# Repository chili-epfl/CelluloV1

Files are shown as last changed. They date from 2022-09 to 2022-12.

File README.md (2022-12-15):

# Cellulo V1

Cellulo is a social, cognitive-motor assistive tabletop robot, created in the CHILI Lab at EPFL. It was born under the efforts of multiple collaborators, with special remarks to [Ayberk Özgür](https://github.com/ayberkozgur) who presented it as his [Ph.D. thesis](https://infoscience.epfl.ch/record/234374?ln=en).

<p align="center">
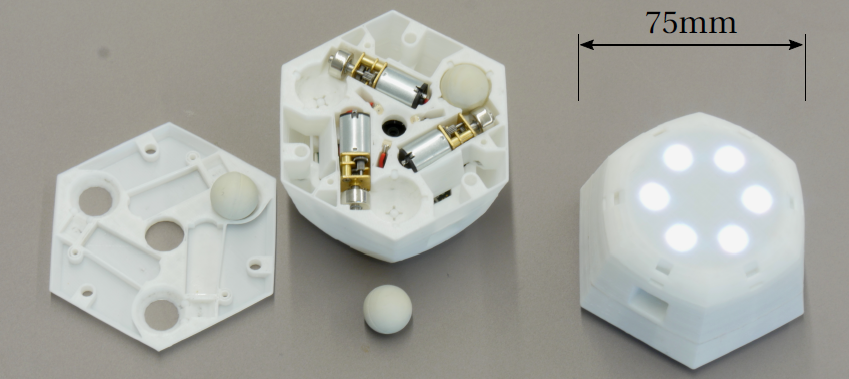
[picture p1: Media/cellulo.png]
  
</p>

## Features

- Holonomic movement
- Haptic feedback
- Sub-mm localization
- LED indicators
- Touch sensor
- Wireless connectivity

## Links

Information about how to work with Cellulo and installations can be found in the [wiki](https://github.com/chili-epfl/cellulo/wiki/Cellulo-V1)

To work with Cellulo it is necesary to install [Cellulo qml plugin](https://github.com/chili-epfl/cellulo-qml-plugin)

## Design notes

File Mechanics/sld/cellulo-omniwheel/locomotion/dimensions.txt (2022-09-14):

"wheel_dia"=30
"wheel_rim_room"=1
"miniwheel_top_bottom_room"=0.7
"miniwheel_side_room"=0.7
"miniwheel_axle_dia"=1.4
"miniwheel_axle_holding_room"=0.5
"rim_extra_width"=0.3
"miniwheel_neck_width"=0.8
"middle_thickness"=8.5
"motor_axle_dia"=3
"motor_axle_room"=0.1
"motor_axle_notch_thickness"=2.5
"mate_room"=0.10
"vertical_mate_room"=0.1
"miniwheel_base_dia"=7.39
"miniwheel_axle_room"=0.1
"miniwheel_rubber_thickness"=1

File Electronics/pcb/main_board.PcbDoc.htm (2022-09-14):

Reporting Options

# File in Previous Format

Date | : | 20/05/2022
Time | : | 18:22:09
Filename | : | C:\Users\VIctor work\Documents\EPFL\CHILI\cellulo-electronics\pcb\main_board.PcbDoc

Version | Warning

This file was generated by an earlier version of the software

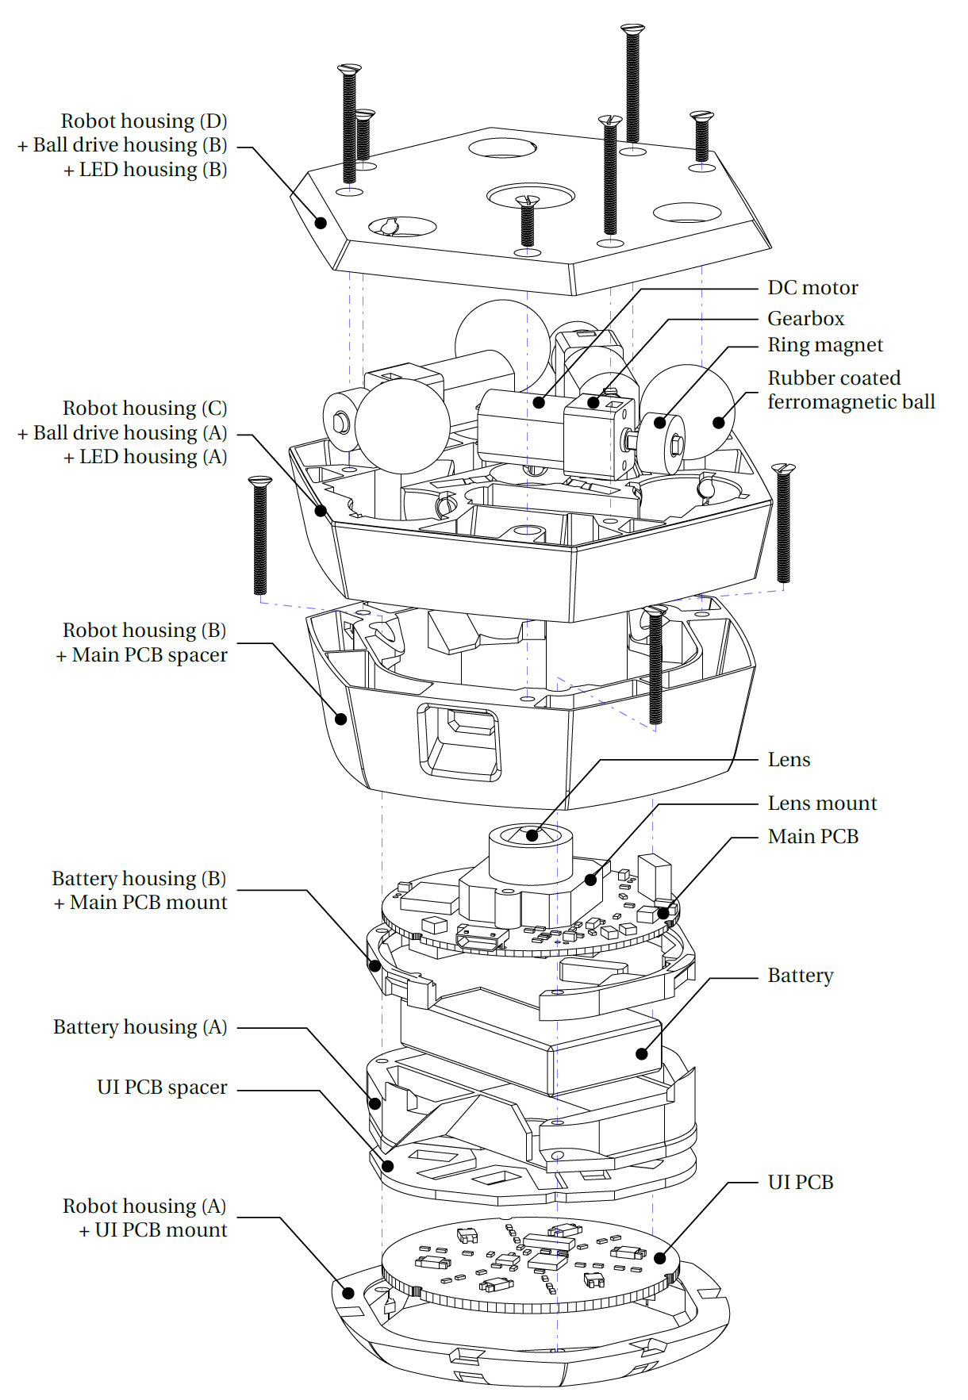
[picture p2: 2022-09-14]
Media/exploited view.png

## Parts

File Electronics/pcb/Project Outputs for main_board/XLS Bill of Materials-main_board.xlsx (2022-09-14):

Designator | Comment | Package | Quantity | Place_YES/NO | Provided_by_customer_YES/NO | Remarks_customer
BAT1 | Battery_1S | WAGO 2059-302 | 1 | YES | YES
C1, C2, C3, C4, C5, C6, C21, C22, C23, C24 | 0.1uF | 1608[0603]_M | 10 | YES | YES
C7, C8, C9 | 47uF | 2012[0805]_M | 3 | YES | YES
C10, C11, C13, C16, C17 | 4.7uF, 10V | 1608[0603]_M | 5 | YES | YES
C12, C15 | 10uF, 10V | 1608[0603]_M | 2 | YES | YES
C14 | 0.1uF, 10V | 1608[0603]_M | 1 | YES | YES
C18, C19, C20 | Unpopulated | 2012[0805]_M | 3 | NO
IC1 | RN42-I/RM | RN42 | 1 | YES | YES
IC2 | PIC32MZ1024ECG064-I/PT | TQFP-64_M | 1 | YES | YES
IC3, IC4, IC5 | BD6210HFP | HRP7_N | 3 | YES | YES
IC6 | MT9V034C12STM | CLCC-48_m | 1 | YES | YES
IC7 | MCP73871-2CCI/ML | QFN-20_M | 1 | YES | YES
IC8 | LM3671MF-3.3 | SOT23-5_N | 1 | YES | YES
IC9 | BQ29700DSET | WSON-6_M | 1 | YES | YES
IC10 | LP2980-AIM5-3.3 | SOT23-5_N | 1 | YES | YES
L1 | SRN2512-2R2M | 2520[1008]_N | 1 | YES | YES
LED1, LED2, LED3 | Unpopulated | PLCC2_WITH_HEATSINK | 3 | NO
M1, M2, M3 | Unpopulated | CABLE-TERMINAL1x2 | 3 | NO
P1 | Connector 5 | BM05B-SRSS_N | 1 | YES | YES
P2 | Connector 12 | FH33-12S-0.5SH_N | 1 | YES | YES
P3 | MicroUSB2.0 | USB3076_M | 1 | YES | YES
Q1 | BSS138BK | SOT23-3_N | 1 | YES | YES
Q2, Q3 | Unpopulated | SOT23-3_N | 2 | NO
Q4, Q5 | CSD17527Q5A | PG-TDSON-8_MOSFET_M | 2 | YES | YES
R1, R2, R3, R4, R5, R8, R10, R11, R12, R13, R14, R15, R16, R19, R24, R28, R29, R30, R34, R43 | 10K | 1608[0603]_M | 20 | YES | YES
R6, R7 | 1K5 | 1608[0603]_M | 2 | YES | YES
R9, R36, R37, R39, R40, R44 | Unpopulated | 1608[0603]_M | 6 | NO
R17, R18 | 1K | 1608[0603]_M | 2 | YES | YES
R20, R21, R22 | 26R1, 0.1%, 1/8W | 2012[0805]_M | 3 | YES | YES
R23, R35 | 330 | 1608[0603]_M | 2 | YES | YES
R25, R27, R31 | 100K | 1608[0603]_M | 3 | YES | YES
R26 | 270K | 1608[0603]_M | 1 | YES | YES
R32 | 1K69 | 1608[0603]_M | 1 | YES | YES
R33 | 16K9 | 1608[0603]_M | 1 | YES | YES
R38 | 2K2 | 1608[0603]_M | 1 | YES | YES
R41, R42 | 5M1 | 1608[0603]_M | 2 | YES | YES

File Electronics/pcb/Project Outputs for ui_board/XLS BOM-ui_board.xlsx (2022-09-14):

Designator | Comment | Package | Quantity | Place_YES/NO | Provided_by_customer_YES/NO | Remarks_customer
C1, C14 | 0.1uF | 1608[0603]_M | 2 | YES | YES
C2, C3, C4, C5, C6, C7, C8, C9, C10, C11, C12, C13, C15, C16, C17, C18, C19, C20 | 10nF | 1608[0603]_M | 18 | YES | YES
IC1 | AT42QT1070-MMH | VQFN-20-EXPOSED-PAD_M | 1 | YES | YES
IC2 | TLC5947 | VQFN-32_M | 1 | YES | YES
K0, K1, K2, K3, K4, K5 | SELF-CAP-TOUCH-SENSOR-PAD | TOUCH_SENSOR_SEED | 6 | NO
LED0, LED1, LED2, LED3, LED4, LED5 | ASMB-MTB0-0A3A2 reverse mount as through hole | PLCC4-REVERSE-MOUNT_N | 6 | YES | YES | Reverse mount as THT
P1 | Connector 12 | FH33-12S-0.5SH_N | 1 | YES | YES
R1, R4, R5, R6, R7, R8 | 4K7 | 1608[0603]_M | 6 | YES | YES
R2, R3 | 47K | 1608[0603]_M | 2 | YES | YES
R9 | 4K99 | 1608[0603]_M | 1 | YES | YES

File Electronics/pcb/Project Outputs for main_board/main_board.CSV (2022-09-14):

Bill of Material for
On 9/11/2017 at 11:02:20 AM
Comment | Pattern | Quantity | Components
0.1uF, 10V | 1608[0603]_M | 1 | C14 | Generic Capacitor
0.1uF | 1608[0603]_M | 10 | C1, C2, C3, C4, C5, C6, C21, C22, C23, C24 | Generic Capacitor
100K | 1608[0603]_M | 3 | R25, R27, R31 | Generic Resistor
10K | 1608[0603]_M | 20 | R1, R2, R3, R4, R5, R8, R10, R11, R12, R13, R14, R15, R16, R19, R24, R28, R29, R30, R34, R43 | Generic Resistor
10uF, 10V | 1608[0603]_M | 2 | C12, C15 | Generic Capacitor
16K9 | 1608[0603]_M | 1 | R33 | Generic Resistor
1K | 1608[0603]_M | 2 | R17, R18 | Generic Resistor
1K5 | 1608[0603]_M | 2 | R6, R7 | Generic Resistor
1K69 | 1608[0603]_M | 1 | R32 | Generic Resistor
26R1, 0.1%, 1/8W | 2012[0805]_M | 3 | R20, R21, R22 | Generic Resistor
270K | 1608[0603]_M | 1 | R26 | Generic Resistor
2K2 | 1608[0603]_M | 1 | R38 | Generic Resistor
330 | 1608[0603]_M | 2 | R23, R35 | Generic Resistor
4.7uF, 10V | 1608[0603]_M | 5 | C10, C11, C13, C16, C17 | Generic Capacitor
47uF | 2012[0805]_M | 3 | C7, C8, C9 | Generic Capacitor
5M1 | 1608[0603]_M | 2 | R41, R42 | Generic Resistor
Battery_1S | WAGO 2059-302 | 1 | BAT1 | Generic single cell battery
BD6210HFP | HRP7_N | 3 | IC3, IC4, IC5 | DC Motor driver, full H-bridge
BQ29700DSET | WSON-6_M | 1 | IC9 | Li-Po battery voltage and current protection
BSS138BK | SOT23-3_N | 1 | Q1 | N-channel MOSFET with body diode drawn
Connector 12 | FH33-12S-0.5SH_N | 1 | P2 | Connector 12-Pin
Connector 5 | BM05B-SRSS_N | 1 | P1 | Connector 5-Pin
CSD17527Q5A | PG-TDSON-8_MOSFET_M | 2 | Q4, Q5 | N-channel MOSFET with body diode drawn
LM3671MF-3.3 | SOT23-5_N | 1 | IC8 | 2MHz, 600mA step-down converter
LP2980-AIM5-3.3 | SOT23-5_N | 1 | IC10 | 50 mA, ultra low drop-out voltage regulator
MCP73871-2CCI/ML | QFN-20_M | 1 | IC7 | Li-Po battery charge controller with system load sharing
MicroUSB2.0 | USB3076_M | 1 | P3 | Micro USB 2.0 plug/receptacle, 5-Leads
MT9V034C12STM | CLCC-48_m | 1 | IC6 | 1/3 WVGA CMOS Image Sensor"
PIC32MZ1024ECG064-I/PT | TQFP-64_M | 1 | IC2 | 32-bit Microcontroller
RN42-I/RM | RN42 | 1 | IC1 | Bluetooth 2.1 module
SRN2512-2R2M | 2520[1008]_N | 1 | L1 | Inductor
Unpopulated | 1608[0603]_M | 6 | R9, R36, R37, R39, R40, R44 | Generic Resistor
Unpopulated | 2012[0805]_M | 3 | C18, C19, C20 | Generic Capacitor
Unpopulated | BoardLensMount_M12_22mm | 1 | LensHolder1
Unpopulated | CABLE-TERMINAL1x2 | 3 | M1, M2, M3 | Generic DC motor
Unpopulated | PLCC2_WITH_HEATSINK | 3 | LED1, LED2, LED3 | Generic LED
Unpopulated | SOT23-3_N | 2 | Q2, Q3 | P-channel MOSFET with body diode drawn

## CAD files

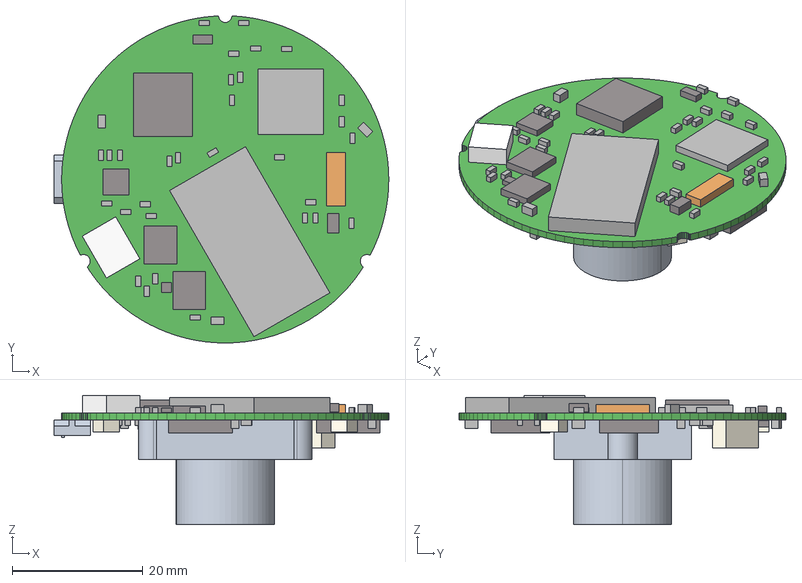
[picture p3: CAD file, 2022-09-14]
Electronics/pcb/Project Outputs for main_board/3D Board Model/main_board.step
51.2 x 50.0 x 19.8 mm
Board
usb3076
Extruded x 90
boad_lens_mount_22mm_hole_distance

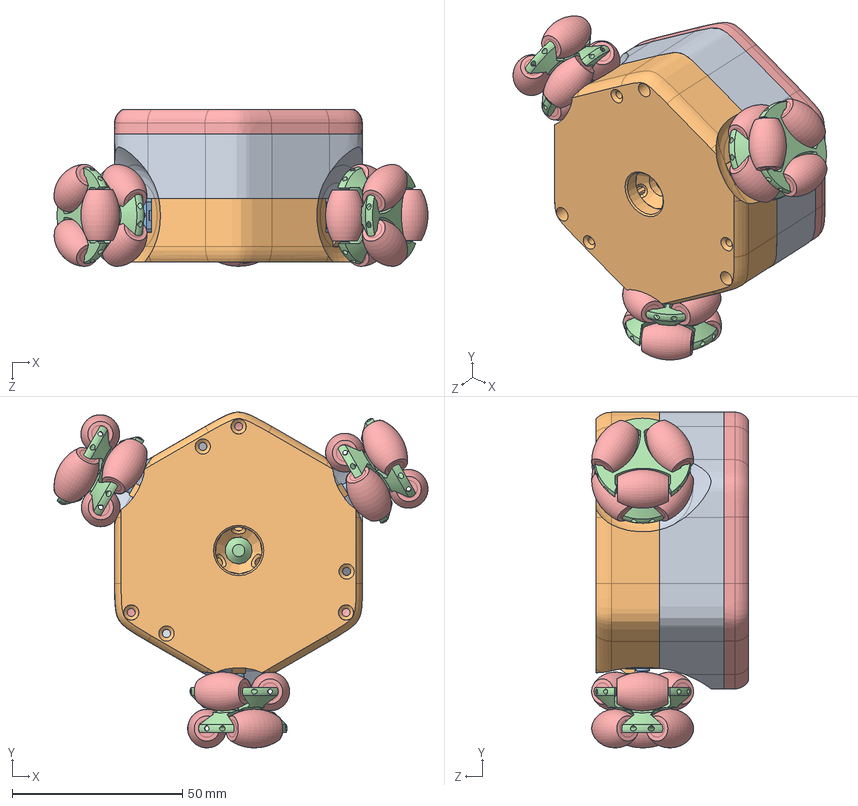
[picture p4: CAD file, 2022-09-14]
Mechanics/sld/cellulo-omniwheel/cellulo-omniwheel.SLDASM
110.0 x 98.7 x 46.1 mm
battery-holder
main-board
fs-blh005
hyp0710
top-omniwheel
ui-board
nut-m2 x 3
top-pcb-cover
middle-cover-omniwheel
omniwheel-drive
pololu-micro-metal-gear-motor x 3
omniwheel30-base x 3
omniwheel30-miniwheel x 18

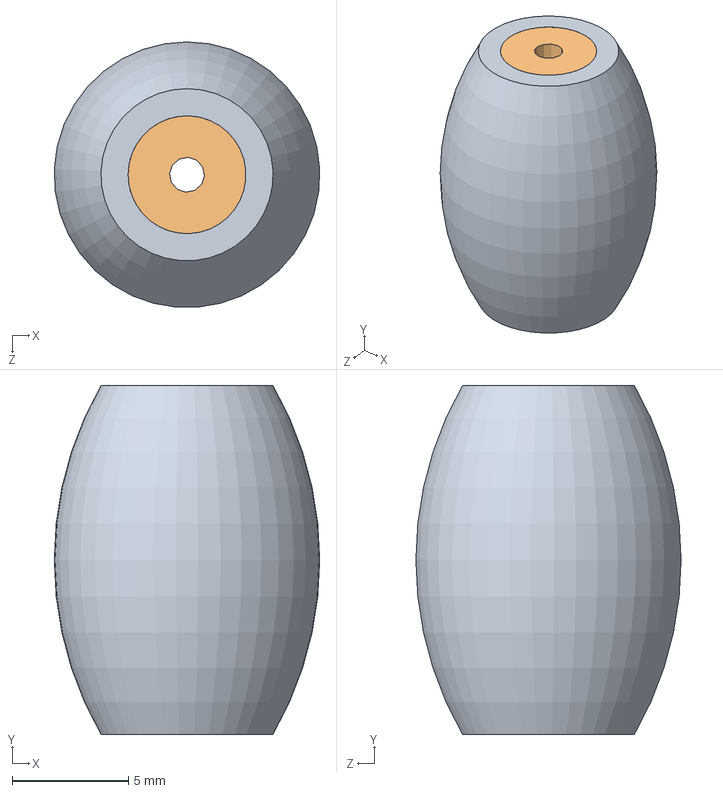
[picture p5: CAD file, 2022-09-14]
Mechanics/sld/cellulo-omniwheel/locomotion/multijet-manufacturing/omniwheel30-miniwheel.SLDASM
11.4 x 15.0 x 11.4 mm
omniwheel30-miniwheel-rubber
omniwheel30-miniwheel-core

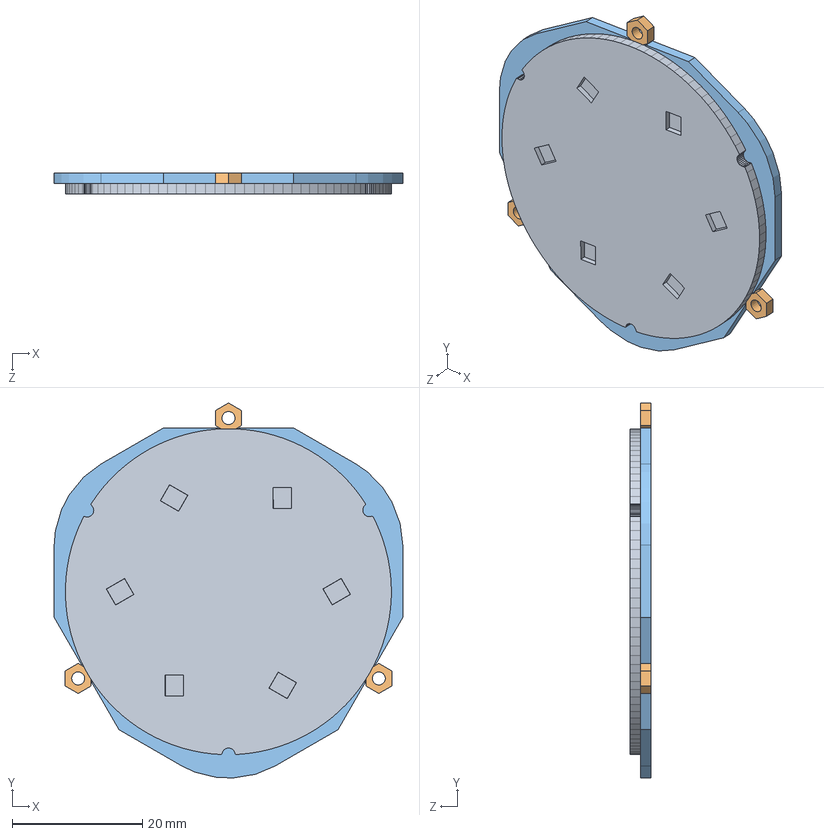
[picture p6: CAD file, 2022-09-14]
Mechanics/sld/cellulo-omniwheel/top/top-assembly-omniwheel.SLDASM
53.5 x 57.5 x 3.20 mm
ui-board
nut-m2 x 3
top-pcb-cover

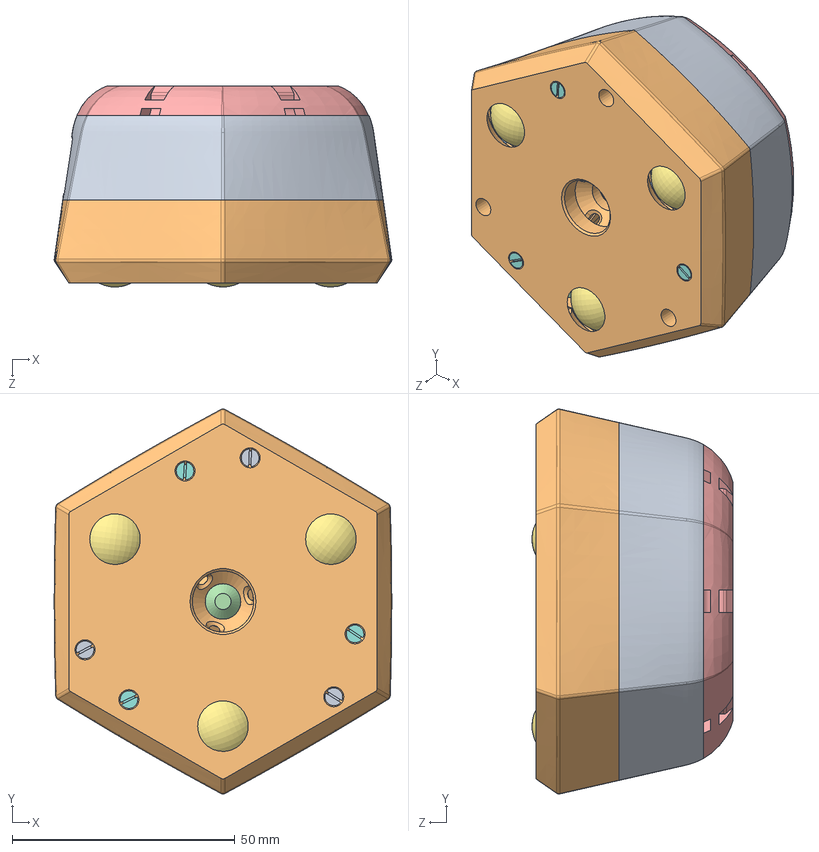
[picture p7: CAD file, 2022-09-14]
Mechanics/sld/cellulo.SLDASM
75.8 x 86.5 x 45.2 mm
battery-holder
main-board
fs-blh005
hyp0710
top
ui-board
nut-m2 x 9
top-pcb-cover
middle-cover
3-ball-drive-housing
bearing-ball x 12
magnet x 3
motor-shaft-magnet-adapter x 3
pololu-micro-metal-gear-motor x 3
spherical-wheel x 3
screw-countersink-m2-20 x 6
screw-countersink-m2-8 x 3

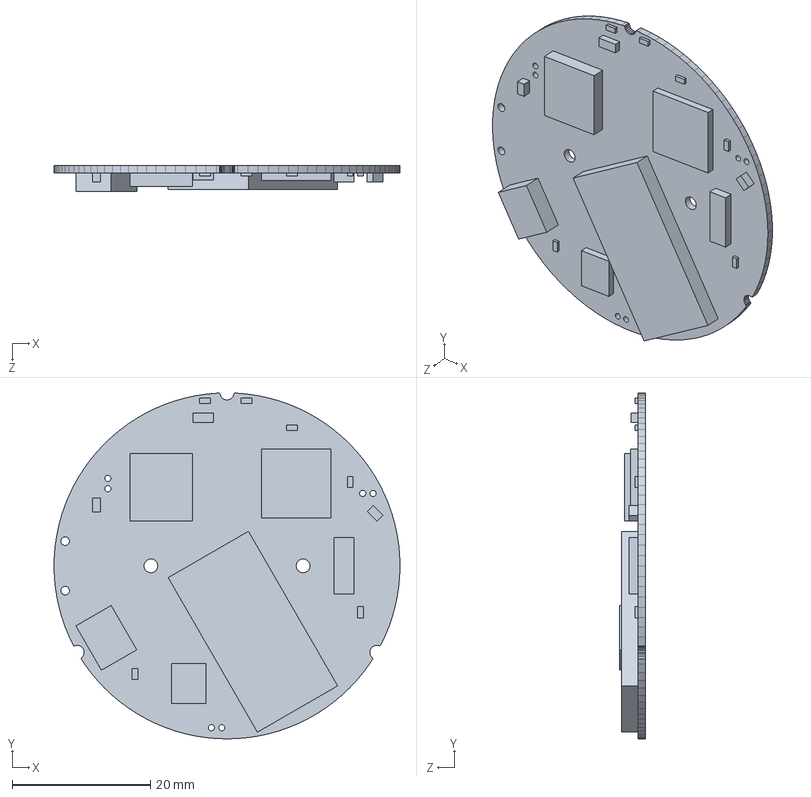
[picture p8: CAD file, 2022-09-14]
Mechanics/sld/pcb/main-board-substitute.SLDPRT
50.0 x 50.0 x 3.77 mm

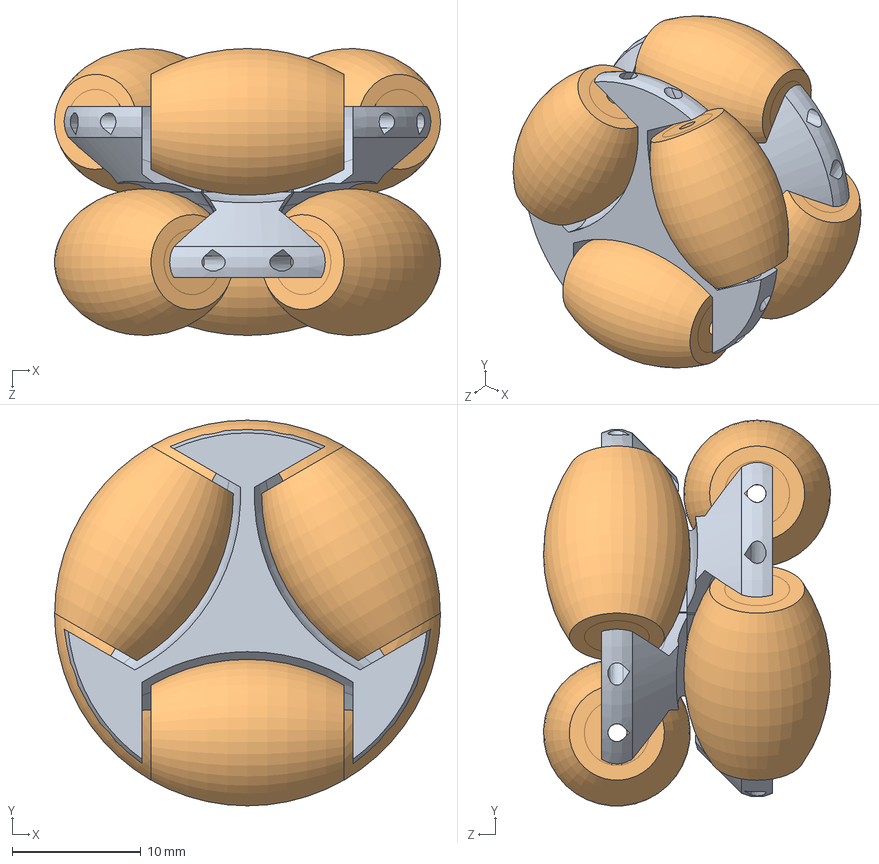
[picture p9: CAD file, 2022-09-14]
Mechanics/sld/cellulo-omniwheel/locomotion/omniwheel30.SLDASM
30.0 x 30.0 x 22.3 mm
omniwheel30-base
omniwheel30-miniwheel x 6

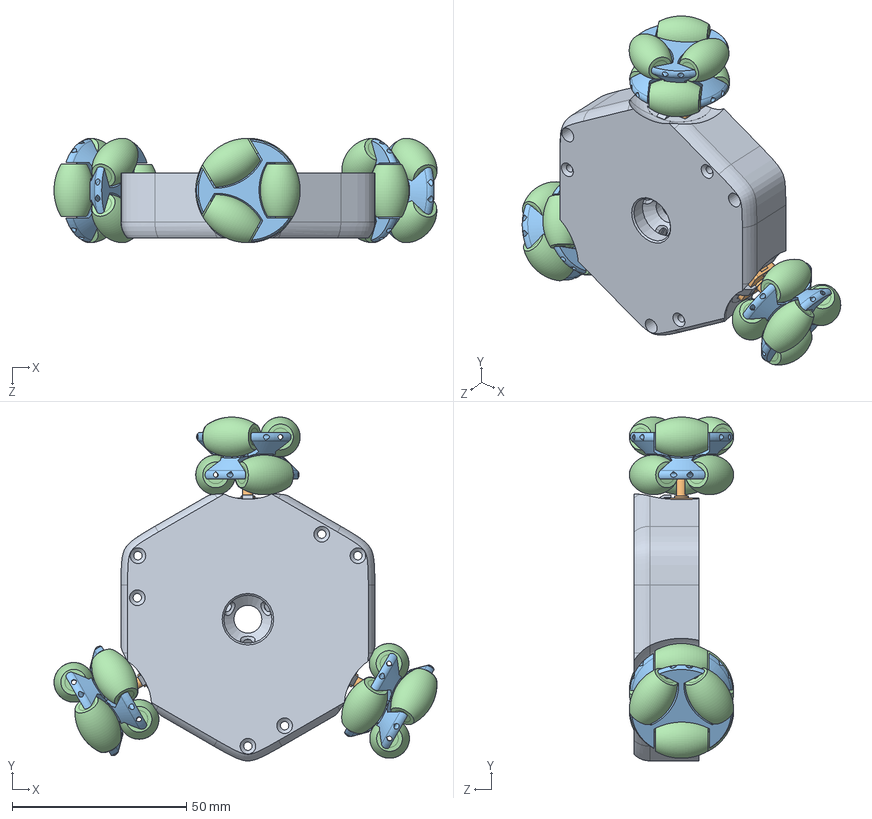
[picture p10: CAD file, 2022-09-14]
Mechanics/sld/cellulo-omniwheel/locomotion/omniwheel-drive.SLDASM
110.0 x 98.8 x 30.0 mm
omniwheel-drive
pololu-micro-metal-gear-motor x 3
omniwheel30-base x 3
omniwheel30-miniwheel x 18

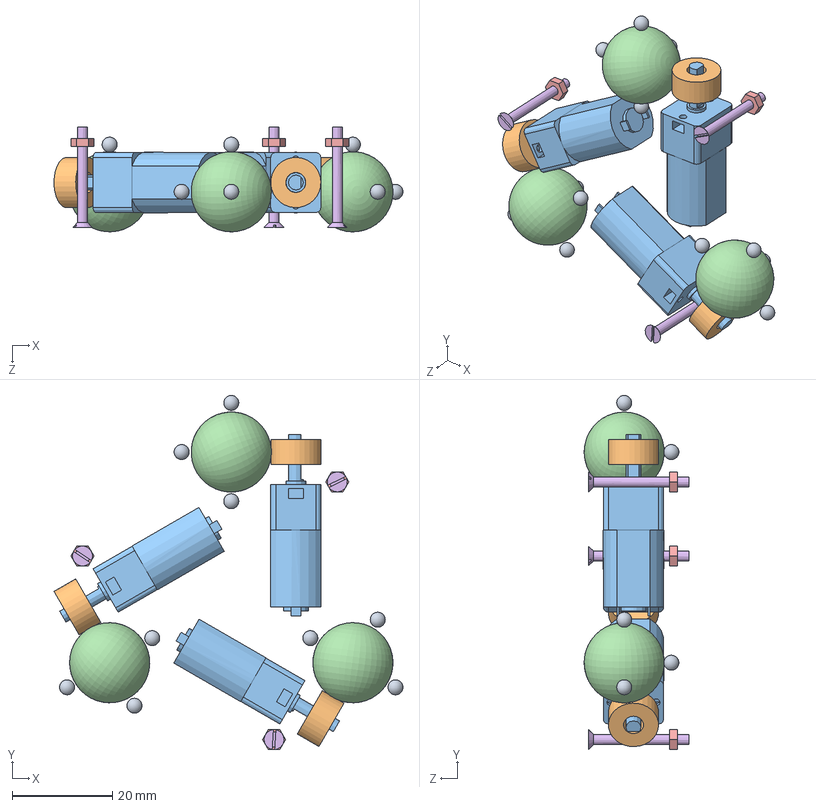
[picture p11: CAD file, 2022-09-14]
Mechanics/sld/locomotion/3-ball-drive.SLDASM
69.6 x 70.6 x 20.9 mm
bearing-ball x 12
magnet x 3
pololu-micro-metal-gear-motor x 3
spherical-wheel x 3
nut-m2 x 3
screw-countersink-m2-20 x 3

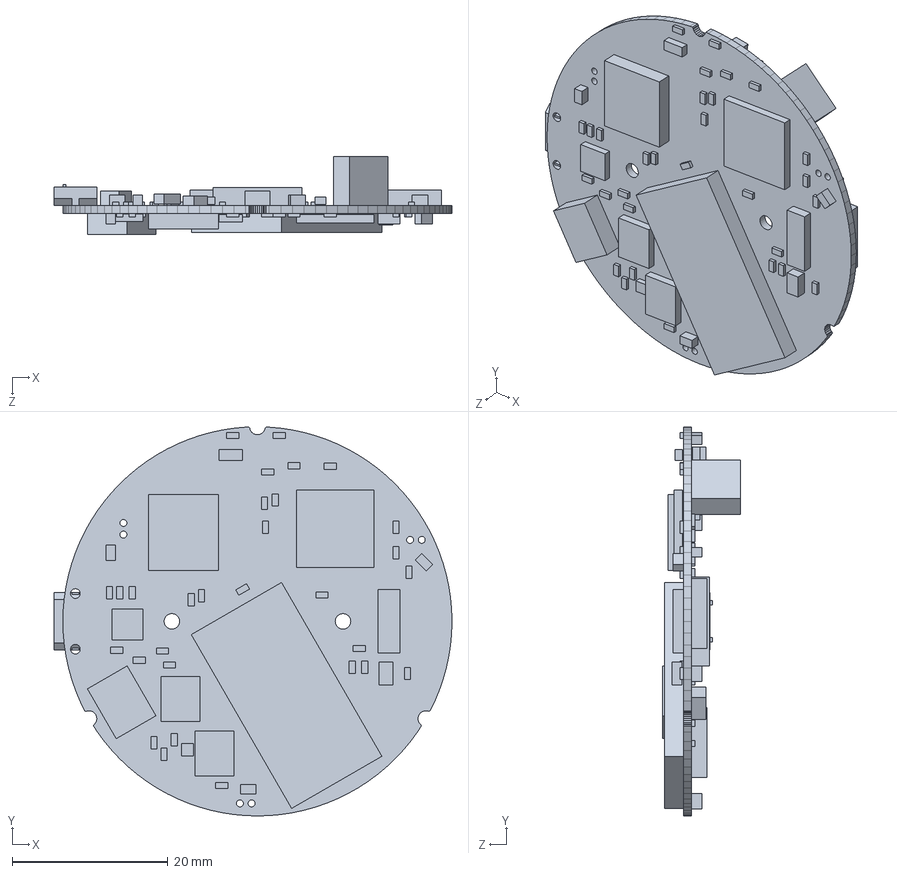
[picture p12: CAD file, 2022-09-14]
Mechanics/sld/pcb/main-board.SLDPRT
51.2 x 50.0 x 10.1 mm

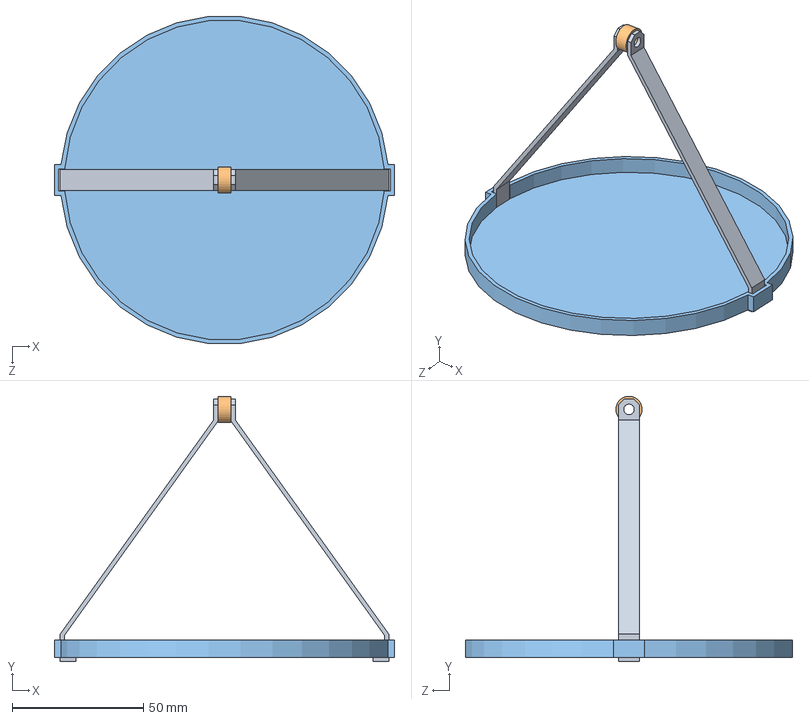
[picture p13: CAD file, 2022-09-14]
Mechanics/sld/util/magnet-force-test-stand/basket.SLDASM
129.5 x 101.0 x 124.4 mm
basket-arm x 2
magnet
basket-base

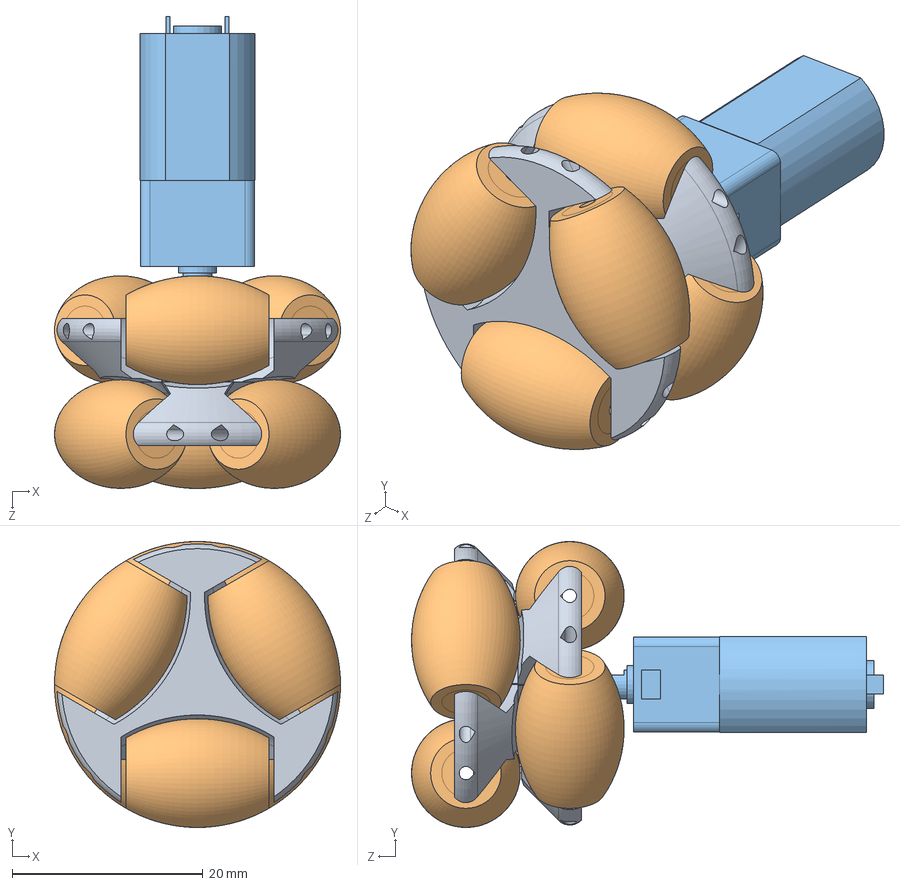
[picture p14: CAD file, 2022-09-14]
Mechanics/sld/cellulo-omniwheel/locomotion/omniwheel30-motor.SLDASM
30.0 x 30.0 x 49.5 mm
omniwheel30-base
omniwheel30-miniwheel x 6
pololu-micro-metal-gear-motor

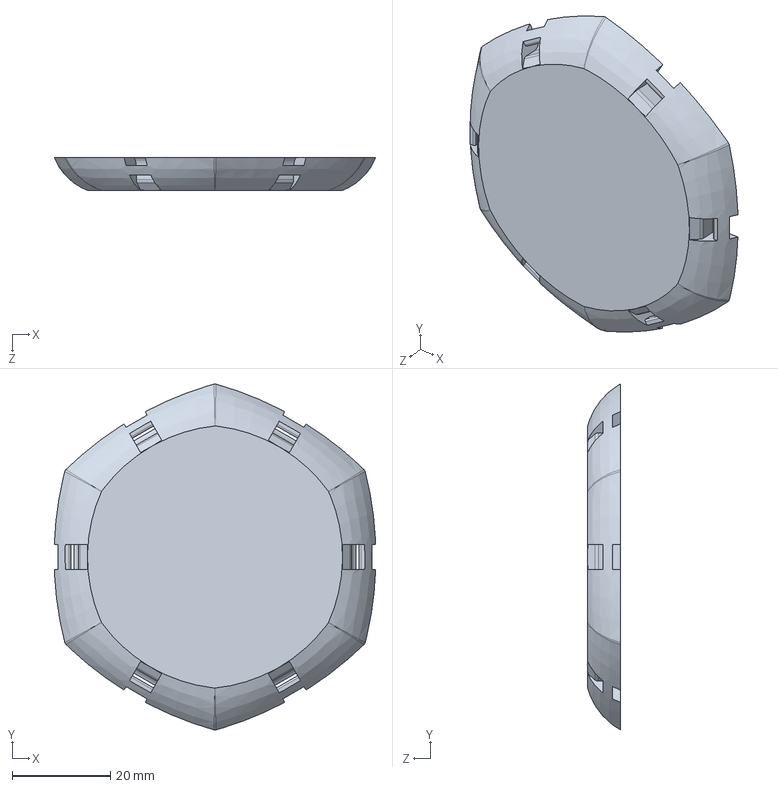
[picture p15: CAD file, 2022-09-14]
Mechanics/sld/top/top-assembly.SLDASM
65.6 x 70.6 x 6.70 mm
top
ui-board
nut-m2 x 3
top-pcb-cover

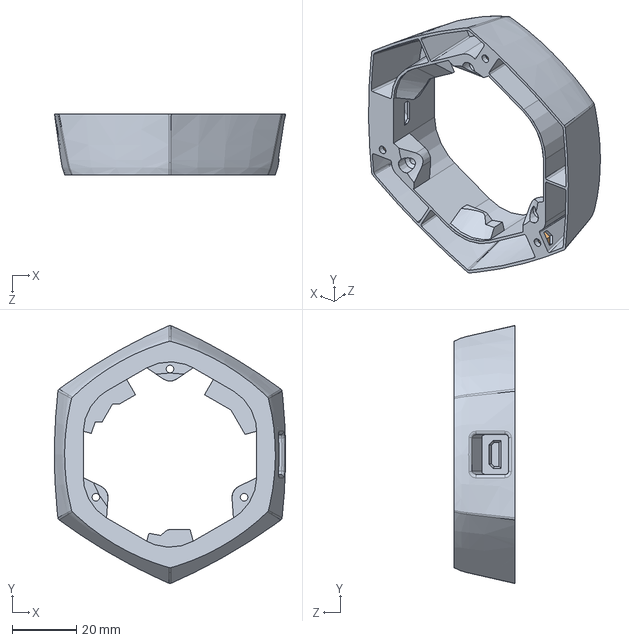
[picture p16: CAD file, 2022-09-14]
Mechanics/sld/middle/middle-cover-assembly.SLDASM
72.0 x 80.4 x 18.9 mm
middle-cover
nut-m2 x 3

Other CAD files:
Mechanics/stl/util/main-board-substitute.STL
Mechanics/sld/middle/middle-assembly.SLDASM
Mechanics/sld/util/magnet-force-test-stand/magnet-force-test-stand.SLDASM
Electronics/pcb/Project Outputs for ui_board/3D Board Model/ui_board.step
Mechanics/model/cellulo-model-hi-poly.STL
Mechanics/model/cellulo-model-low-poly.STL
Mechanics/model/cellulo-model.SLDPRT
Mechanics/sld/cellulo-omniwheel/locomotion/multijet-manufacturing/omniwheel30-miniwheel-core.SLDPRT
Mechanics/sld/cellulo-omniwheel/locomotion/multijet-manufacturing/omniwheel30-miniwheel-rubber.SLDPRT
Mechanics/sld/cellulo-omniwheel/locomotion/omniwheel-drive.SLDPRT
Mechanics/sld/cellulo-omniwheel/locomotion/omniwheel20-miniwheel-print.SLDPRT
Mechanics/sld/cellulo-omniwheel/locomotion/omniwheel20.SLDPRT
Mechanics/sld/cellulo-omniwheel/locomotion/omniwheel30-base.SLDPRT
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

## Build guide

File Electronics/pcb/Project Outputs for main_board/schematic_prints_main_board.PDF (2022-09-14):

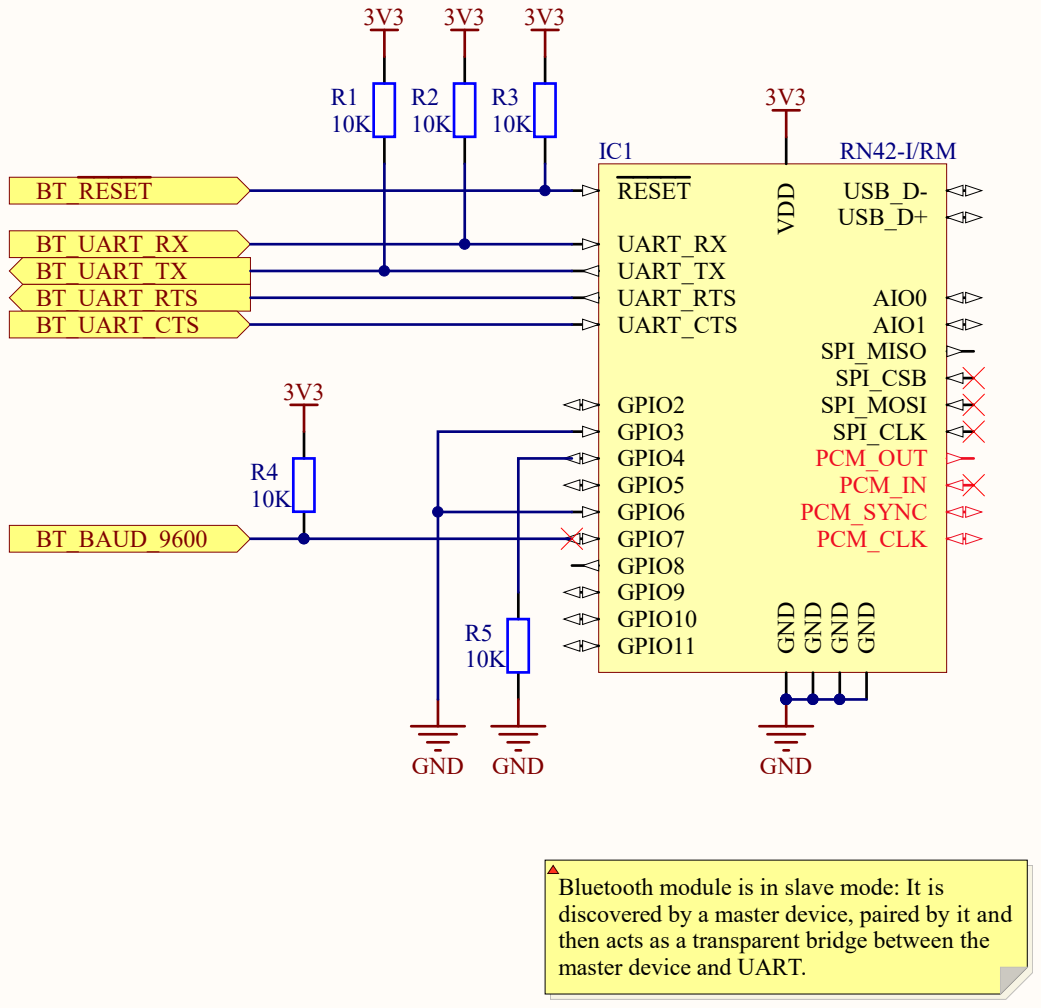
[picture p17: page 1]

Bluetooth module is in slave mode: It is
discovered by a master device, paired by it and
then acts as a transparent bridge between the master device and UART.

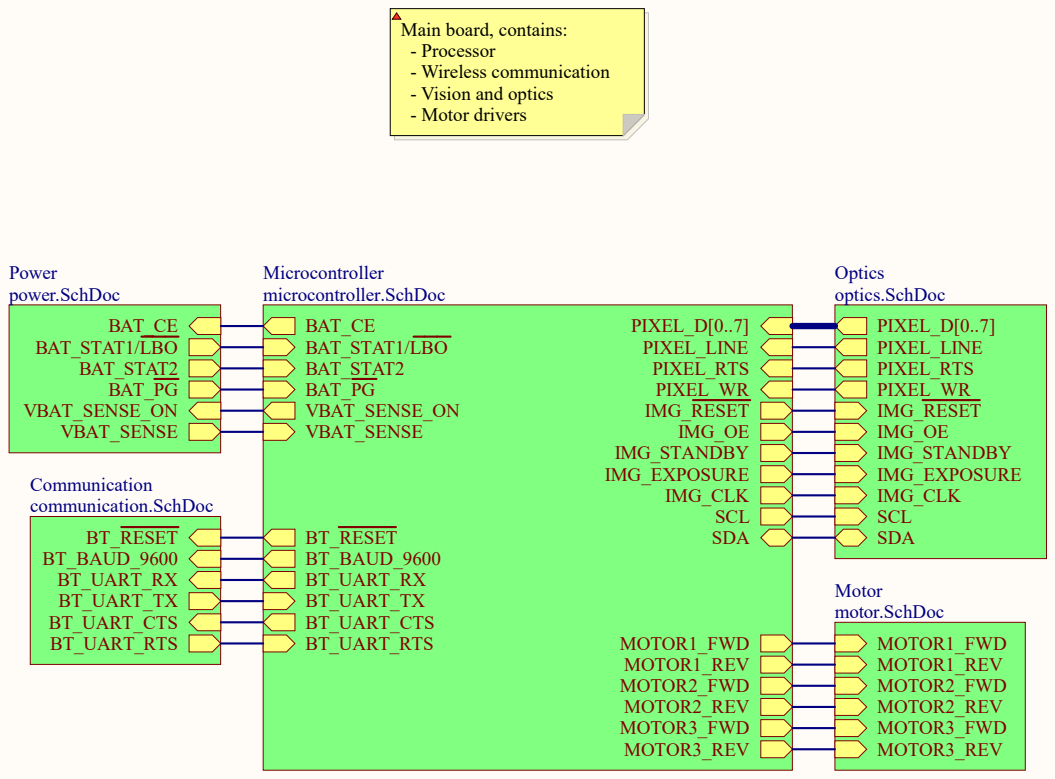
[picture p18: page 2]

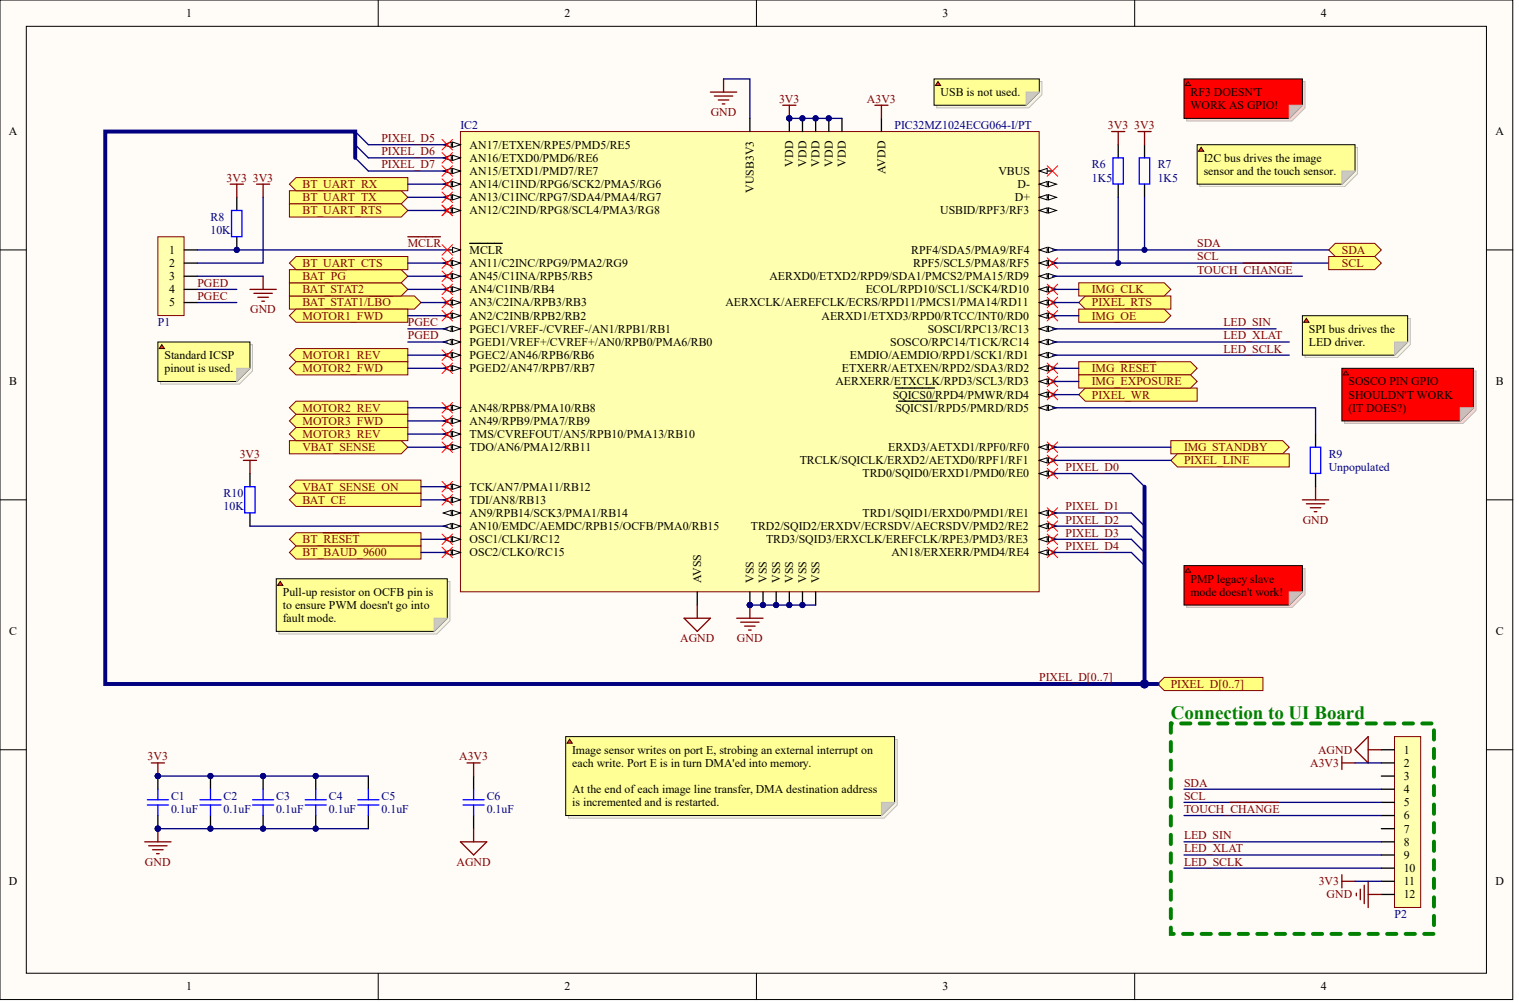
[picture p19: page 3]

USB is not used.

I2C bus drives the imag
sensor and the touch sensor

SPI bus drives the LED driver.

Pull-up resistor on OCFB pin is
to ensure PWM doesn't go into fault mode.

PIXEL_D[0..7]
Connection to UI Board

mage sensor writes on port E, strobing an external interrupt on
each write. Port E is in turn DMA'ed into memory

At the end of each image line transfer, DMA destination address
is incremented and is restarted.

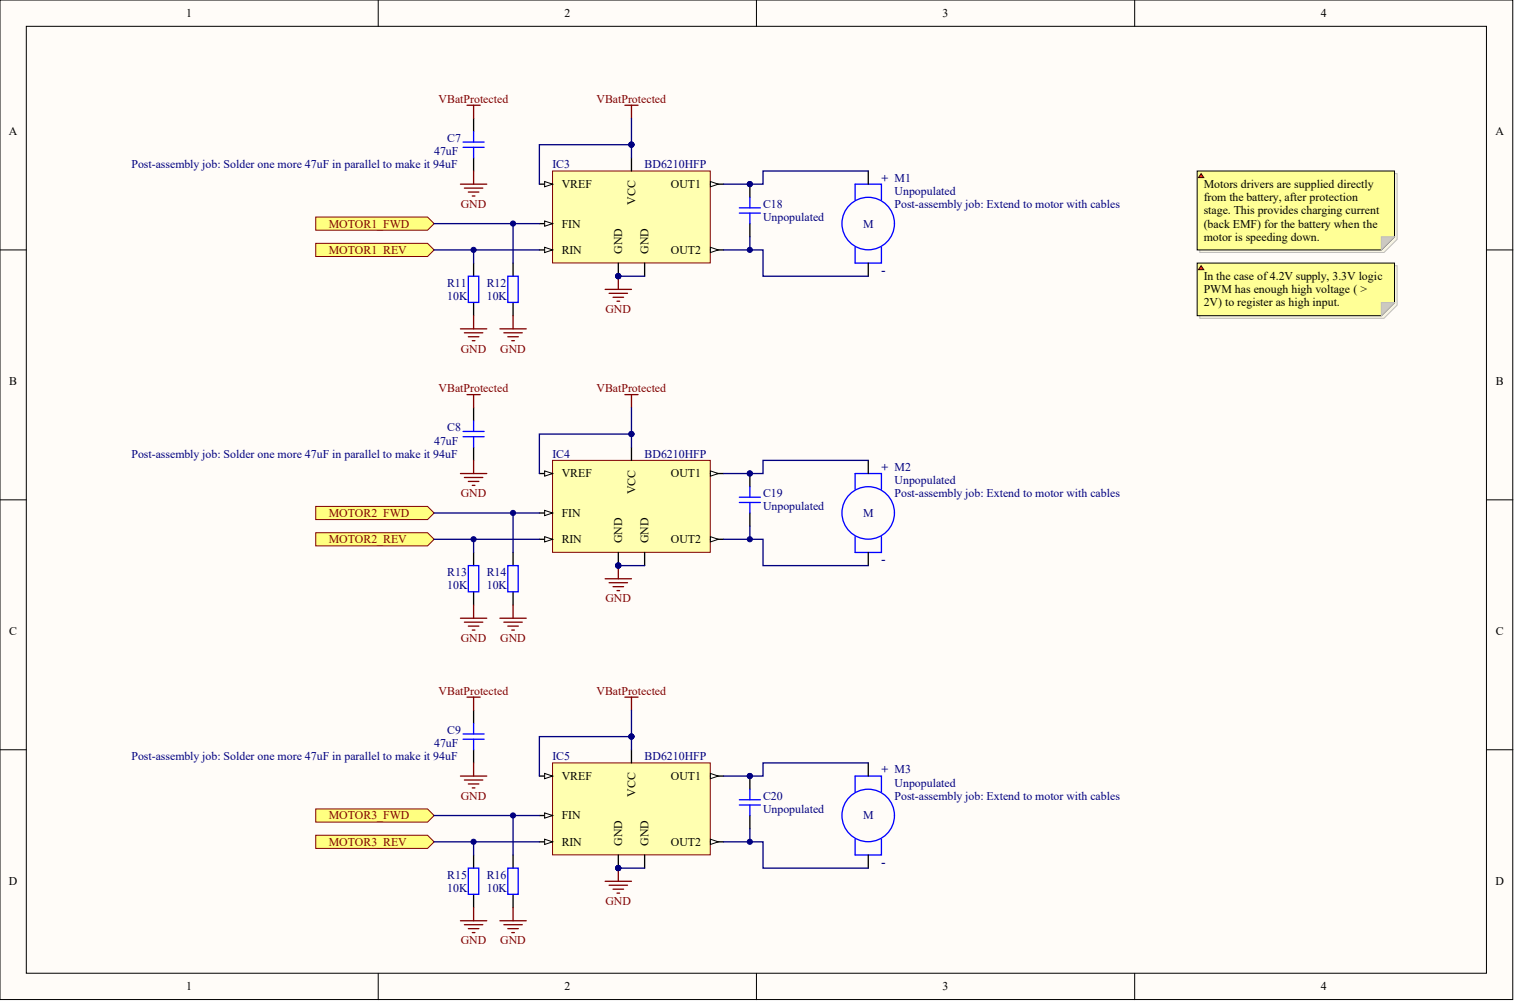
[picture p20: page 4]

Post-assembly job: Solder one more 47uF in parallel to make it 94uF

Motors drivers are supplied directly
from the battery, after protection
stage. This provides charging current
(back EMF) for the battery when the
motor is speeding down.

In the case of 4.2V supply, 3.3V logic
PWM has enough high voltage ( >
2V) to register as high input.

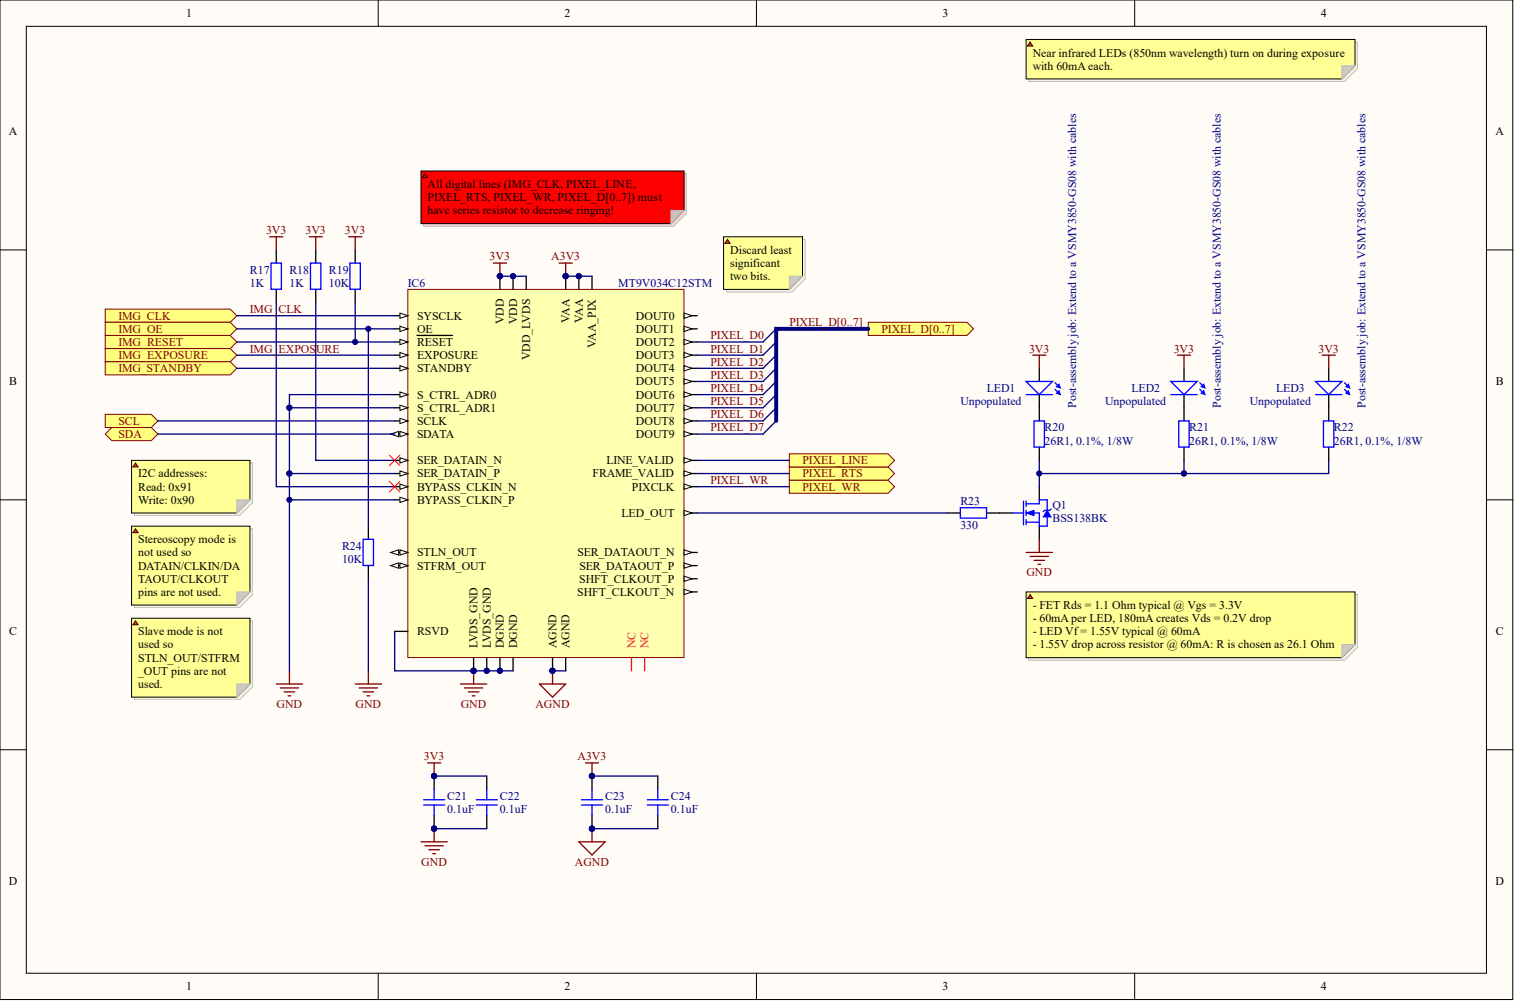
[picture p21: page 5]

Near infrared LEDs (850nm wavelength) turn on during exposure
with 60mA each.

All digital lines (IMG_CLK, PIXEL_LINE,
PIXEL_RTS, PIXEL_WR, PIXEL_D[0..7]) must
have series resistor to decrease ringing!

Stereoscopy mode is
not used so
DATAIN/CLKIN/DA
TAOUT/CLKOUT
pins are not used.

- FET Rds = 1.1 Ohm typical @ Vgs = 3.3V
- 60mA per LED, 180mA creates Vds = 0.2V drop
- LED Vf = 1.55V typical @ 60mA

Slave mode is not
used so
STLN_OUT/STFRM
_OUT pins are not
used.

- 1.55V drop across resistor @ 60mA: R is chosen as 26.1 Ohm

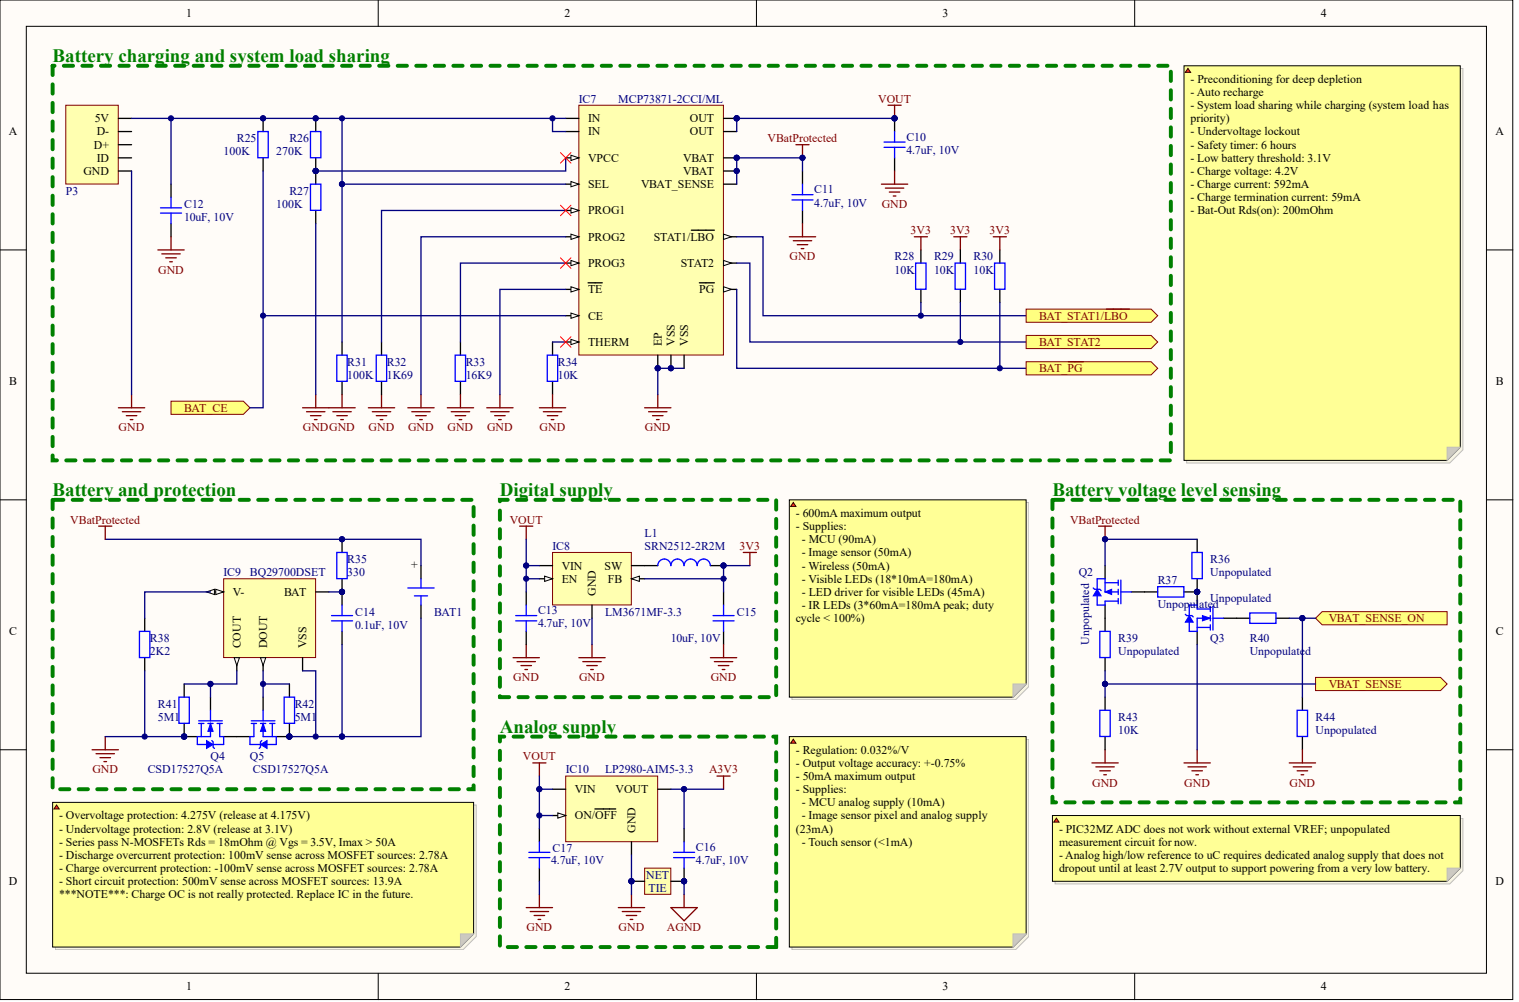
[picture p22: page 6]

Battery charging and system load sharing

- Preconditioning for deep depletion
- Auto recharge
- System load sharing while charging (system load has
priority)
- Undervoltage lockout
- Safety timer: 6 hours
- Low battery threshold: 3.1V
- Charge voltage: 4.2V
- Charge current: 592mA
- Charge termination current: 59mA
- Bat-Out Rds(on): 200mOhm

GND R28 | R29 | R30

- 600mA maximum output
- Supplies:
- MCU (90mA)
- Image sensor (50mA)
- Wireless (50mA)
- Visible LEDs (18*10mA=180mA)
- LED driver for visible LEDs (45mA)
- IR LEDs (3*60mA=180mA peak; duty
cycle < 100%)

- Regulation: 0.032%/V
- Output voltage accuracy: +-0.75%
- 50mA maximum output
- MCU analog supply (10mA)
- Image sensor pixel and analog supply
- Touch sensor (<1mA)

- Overvoltage protection: 4.275V (release at 4.175V)
- Undervoltage protection: 2.8V (release at 3.1V)
- Series pass N-MOSFETs Rds = 18mOhm @ Vgs = 3.5V, Imax > 50A
- Discharge overcurrent protection: 100mV sense across MOSFET sources: 2.78A
- Charge overcurrent protection: -100mV sense across MOSFET sources: 2.78A
- Short circuit protection: 500mV sense across MOSFET sources: 13.9A
***NOTE***: Charge OC is not really protected. Replace IC in the future.

- PIC32MZ ADC does not work without external VREF; unpopulated
measurement circuit for now.
- Analog high/low reference to uC requires dedicated analog supply that does not
dropout until at least 2.7V output to support powering from a very low battery.

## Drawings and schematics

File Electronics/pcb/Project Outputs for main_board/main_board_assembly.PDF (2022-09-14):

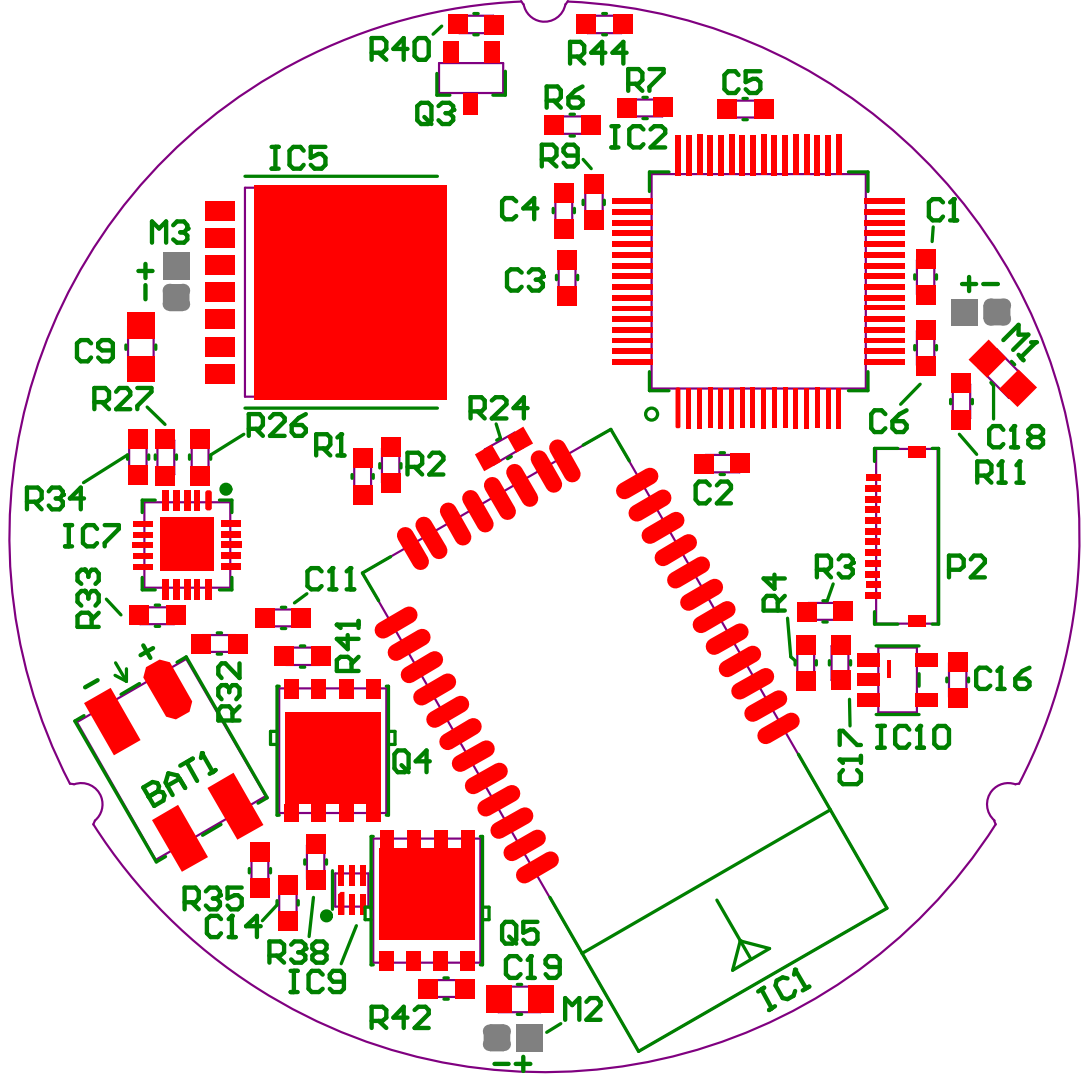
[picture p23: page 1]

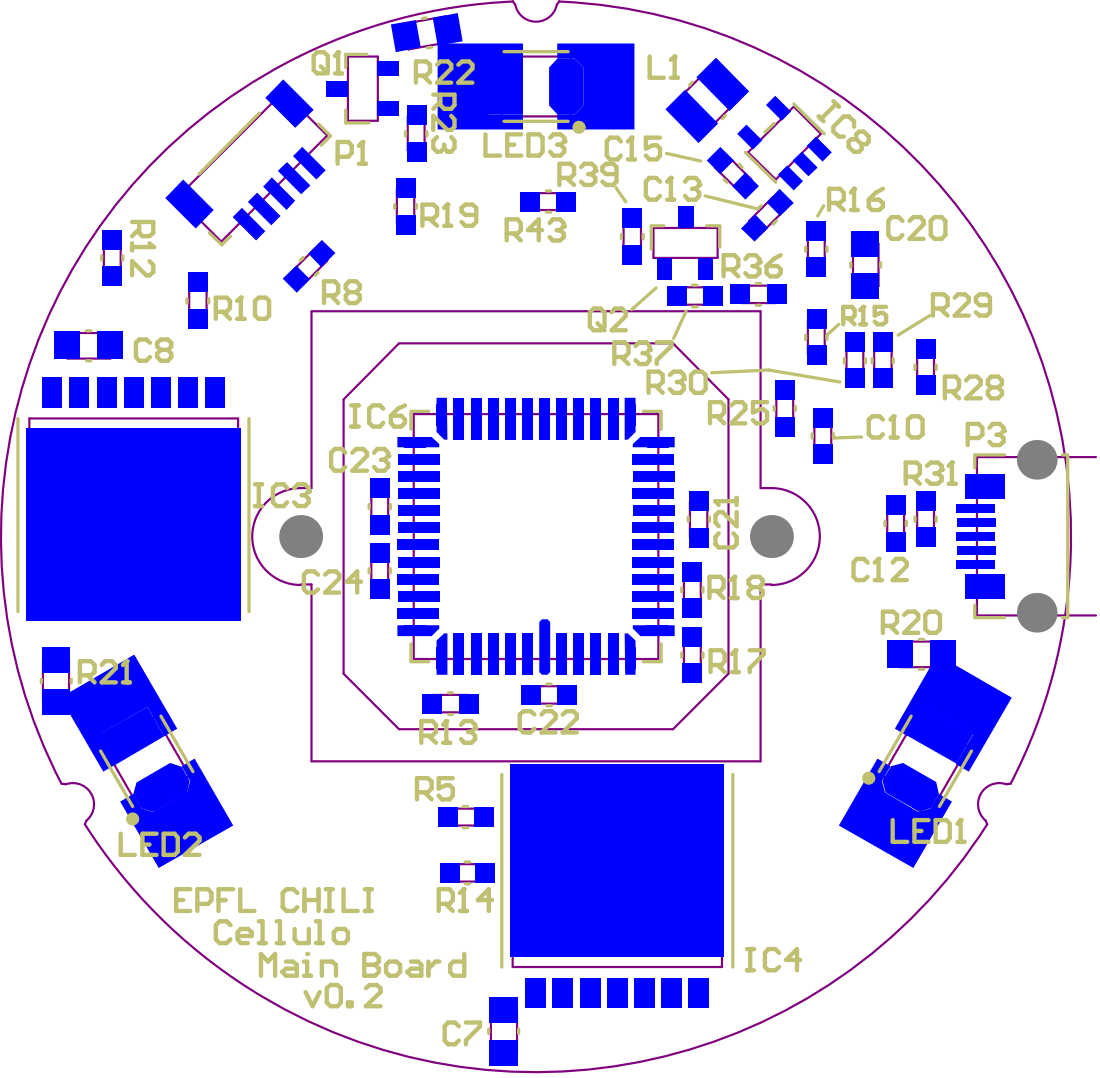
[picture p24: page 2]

Designator | Comment | Footprint | Quantit y
BAT1 | Battery_1S | WAGO 2059-302 | 1
C1, C2, C3, C4, C5, C6, C21, C22, C23, C24 | 0.1uF | 1608[0603]_M | 10
C7, C8, C9 | 47uF | 2012[0805]_M | 3
C10, C11, C13, C16, C17 | 4.7uF, 10V | 1608[0603]_M | 5
C12, C15 | 10uF, 10V | 1608[0603]_M | 2
C14 | 0.1uF, 10V | 1608[0603]_M | 1
C18, C19, C20 | Unpopulated | 2012[0805]_M | 3
IC1 | RN42-I/RM | RN42 | 1
IC2 | PIC32MZ1024ECG06 4-I/PT | TQFP-64_M | 1
IC3, IC4, IC5 | BD6210HFP | HRP7_N | 3
IC6 | MT9V034C12STM | CLCC-48_m | 1
IC7 | MCP73871-2CCI/ML | QFN-20_M | 1
IC8 | LM3671MF-3.3 | SOT23-5_N | 1
IC9 | BQ29700DSET | WSON-6_M | 1
IC10 | LP2980-AIM5-3.3 | SOT23-5_N | 1
L1 | SRN2512-2R2M | 2520[1008]_N | 1
LED1, LED2, LED3 | Unpopulated | PLCC2_WITH_HEATSINK | 3
LensHolder1 | Unpopulated | BoardLensMount_M12_22mm | 1
M1, M2, M3 | Unpopulated | CABLE-TERMINAL1x2 | 3
P1 | Connector 5 | BM05B-SRSS_N | 1
P2 | Connector 12 | FH33-12S-0.5SH_N | 1
P3 | MicroUSB2.0 | USB3076_M | 1
Q1 | BSS138BK | SOT23-3_N | 1
Q2, Q3 | Unpopulated | SOT23-3_N | 2
Q4, Q5 | CSD17527Q5A | PG-TDSON-8_MOSFET_M | 2
R1, R2, R3, R4, R5, R8, R10, R11, R12, R13, R14, R15, R16, R19, R24, R28, R29, R30, R34, R43 | 10K | 1608[0603]_M | 20
R6, R7 | 1K5 | 1608[0603]_M | 2
R9, R36, R37, R39, R40, R44 | Unpopulated | 1608[0603]_M | 6
R17, R18 | 1K | 1608[0603]_M | 2
R20, R21, R22 | 26R1, 0.1%, 1/8W | 2012[0805]_M | 3
R23, R35 | 330 | 1608[0603]_M | 2
R25, R27, R31 | 100K | 1608[0603]_M | 3
R26 | 270K | 1608[0603]_M | 1
R32 | 1K69 | 1608[0603]_M | 1
R33 | 16K9 | 1608[0603]_M | 1
R38 | 2K2 | 1608[0603]_M | 1
R41, R42 | 5M1 | 1608[0603]_M | 2

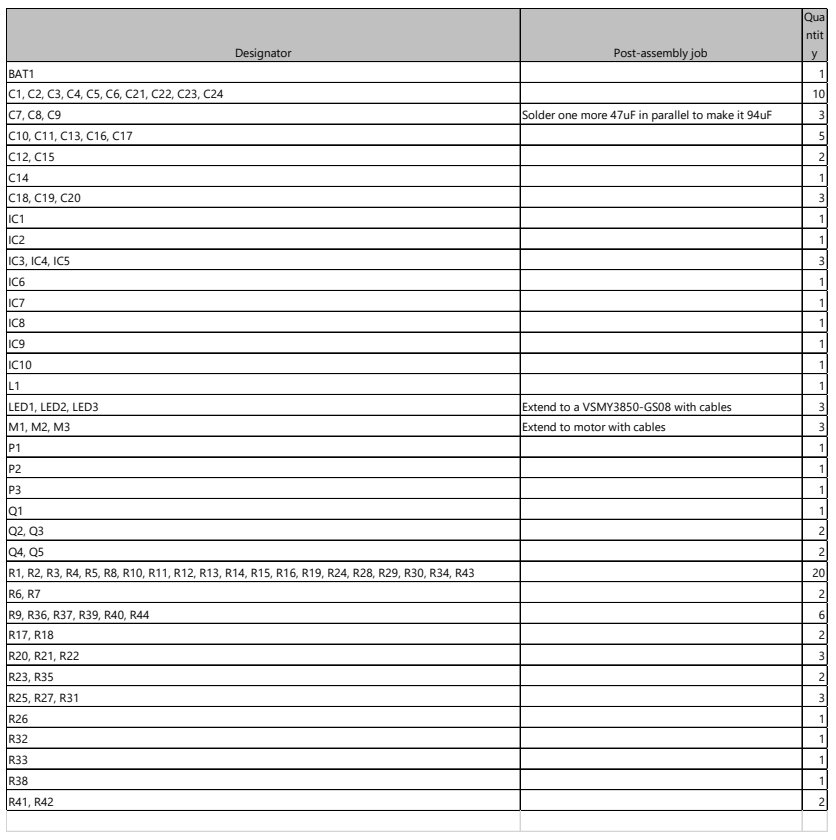
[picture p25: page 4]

Designator | Post-assembly job | Qua ntit y

BAT1 | | 1
C1, C2, C3, C4, C5, C6, C21, C22, C23, C24 | | 10
C7, C8, C9 | Solder one more 47uF in parallel to make it 94uF | 3

C10, C11, C13, C16, C17 | | 5
C12, C15 | | 2
C14 | | 1
C18, C19, C20 | | 3
IC1 | | 1
IC2 | | 1
IC3, IC4, IC5 | | 3
IC6 | | 1
IC7 | | 1
IC8 | | 1
IC9 | | 1
IC10 | | 1
L1 | | 1
LED1, LED2, LED3 | Extend to a VSMY3850-GS08 with cables | 3
M1, M2, M3 | Extend to motor with cables | 3

P1 | | 1
P2 | | 1
P3 | | 1
Q1 | | 1
Q2, Q3 | | 2
Q4, Q5 | | 2
R1, R2, R3, R4, R5, R8, R10, R11, R12, R13, R14, R15, R16, R19, R24, R28, R29, R30, R34, R43 | | 20
R6, R7 | | 2
R9, R36, R37, R39, R40, R44 | | 6
R17, R18 | | 2
R20, R21, R22 | | 3
R23, R35 | | 2
R25, R27, R31 | | 3
R26 | | 1
R32 | | 1
R33 | | 1
R38 | | 1
R41, R42 | | 2

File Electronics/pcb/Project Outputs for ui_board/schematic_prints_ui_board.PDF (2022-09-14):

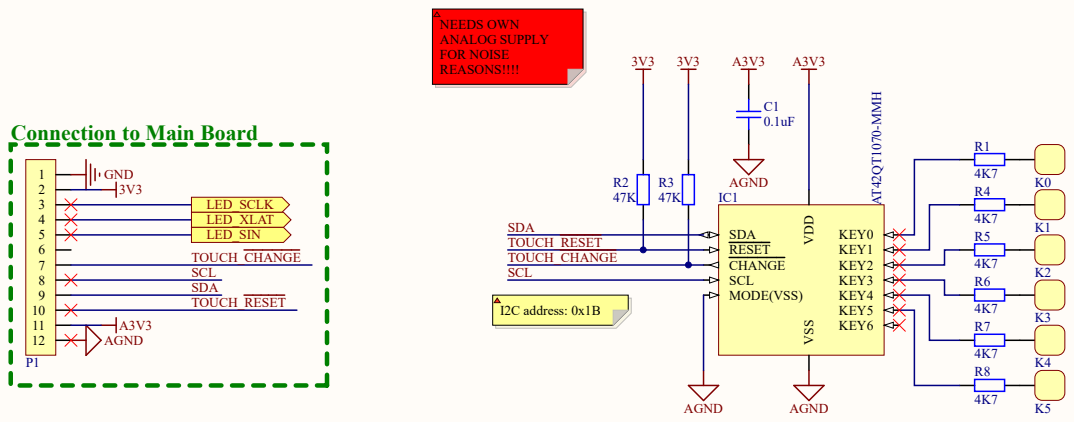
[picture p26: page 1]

Connection to Main Board

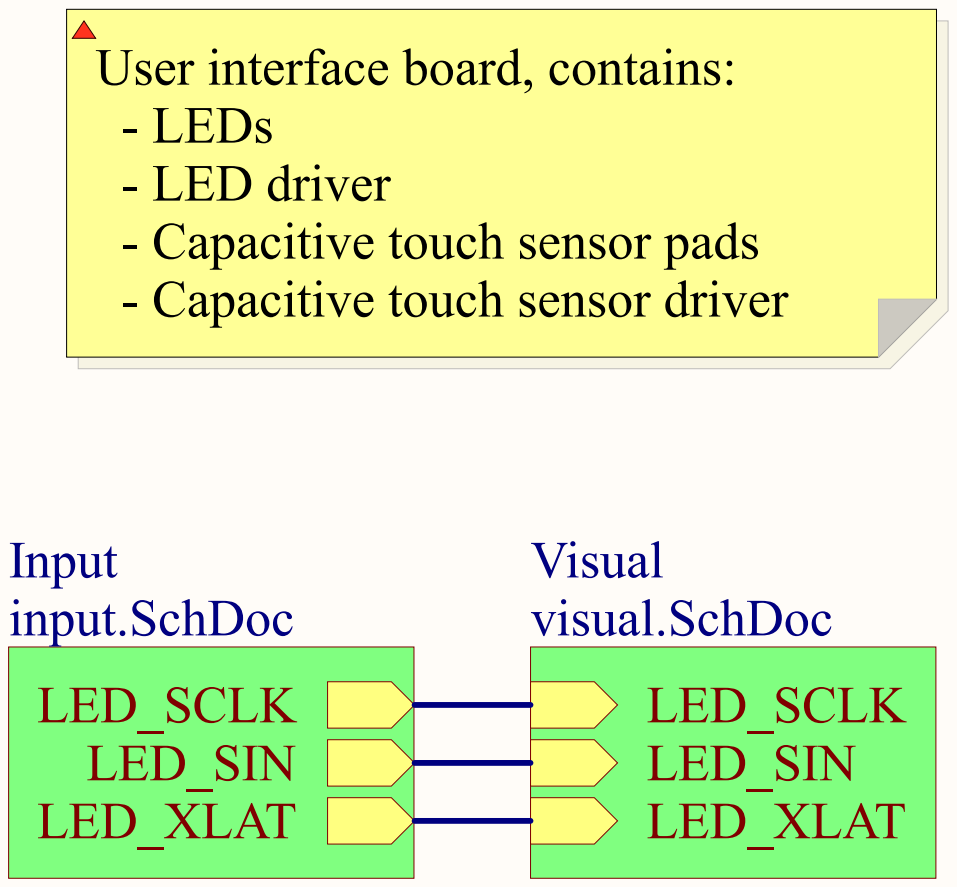
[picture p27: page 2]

User interface board, contains:
- LEDs
- LED driver
- Capacitive touch sensor pads
- Capacitive touch sensor driver

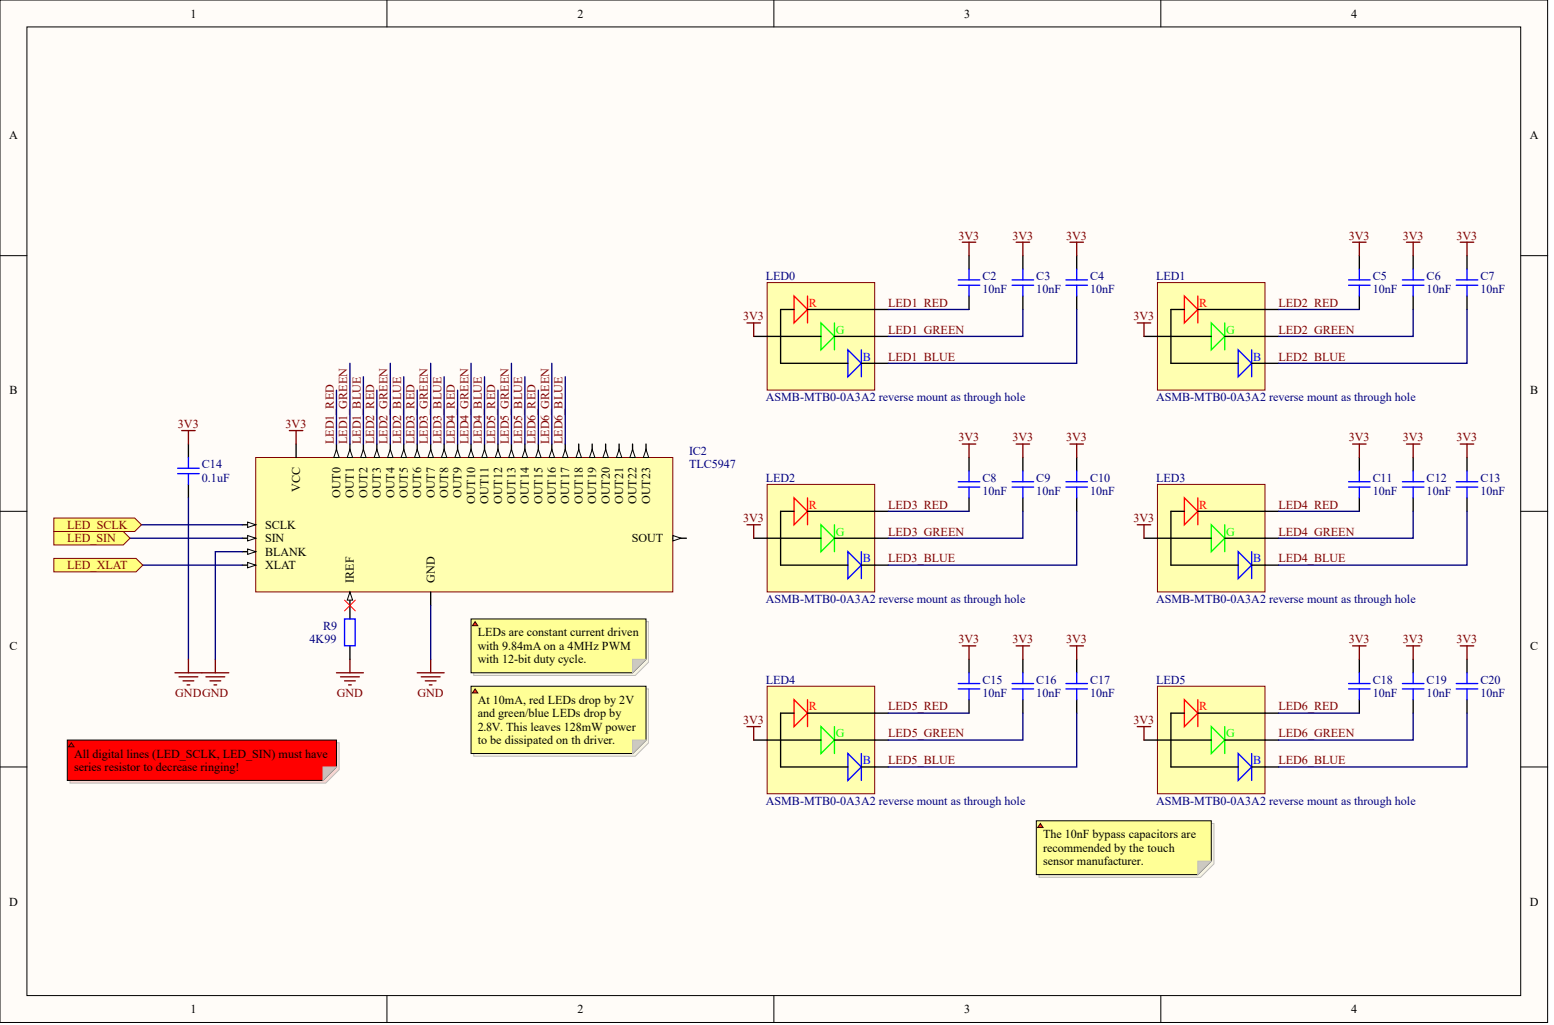
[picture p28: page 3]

ASMB-MTB0-0A3A2 reverse mount as through hole LED1_RED LED1_GREEN LED1_BLUE

ASMB-MTB0-0A3A2 reverse mount as through hole LED2_RED LED2_GREEN LED2_BLUE

ASMB-MTB0-0A3A2 reverse mount as through hole LED3_RED LED3_GREEN LED3_BLUE

ASMB-MTB0-0A3A2 reverse mount as through hole LED4_RED LED4_GREEN LED4_BLUE

LEDs are constant current driven with 9.84mA on a 4MHz PWM with 12-bit duty cycle.

At 10mA, red LEDs drop by 2V
and green/blue LEDs drop by
2.8V. This leaves 128m
to be dissipated on th driver

ASMB-MTB0-0A3A2 reverse mount as through hole LED5_RED LED5_GREEN LED5_BLUE

ASMB-MTB0-0A3A2 reverse mount as through hole LED6_RED LED6_GREEN LED6_BLUE

All digital lines (LED_SCLK, LED_SIN) must hav
series resistor to decrease ringing

The 10nF bypass capacitors are
mended by the touch
recom
sensor manufacturer

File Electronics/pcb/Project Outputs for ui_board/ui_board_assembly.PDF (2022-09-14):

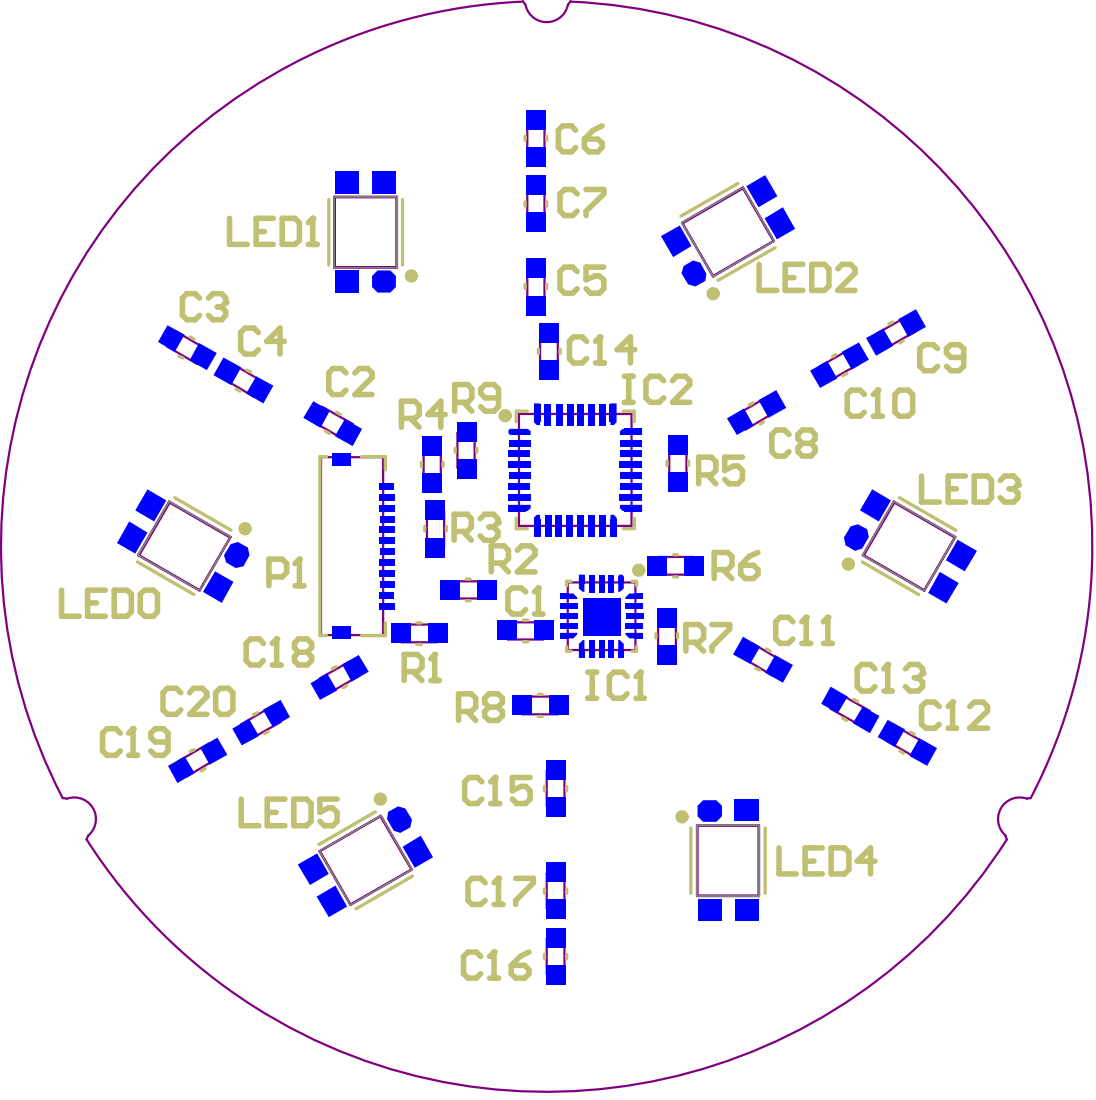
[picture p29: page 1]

Designator | Comment | Footprint | Quan tity
C1, C14 | 0.1uF | 1608[0603]_M | 2
C2, C3, C4, C5, C6, C7, C8, C9, C10, C11, C12, C13, C15, C16, C17, C18, C19, C20 | 10nF | 1608[0603]_M | 18
IC1 | AT42QT1070-MMH | VQFN-20-EXPOSED-PAD_M | 1
IC2 | TLC5947 | VQFN-32_M | 1
K0, K1, K2, K3, K4, K5 | SELF-CAP-TOUCH-SENSOR-PAD | TOUCH_SENSOR_SEED | 6
LED0, LED1, LED2, LED3, LED4, LED5 | ASMB-MTB0-0A3A2 reverse mount as through hole | PLCC4-REVERSE-MOUNT_N | 6
P1 | Connector 12 | FH33-12S-0.5SH_N | 1
R1, R4, R5, R6, R7, R8 | 4K7 | 1608[0603]_M | 6
R2, R3 | 47K | 1608[0603]_M | 2
R9 | 4K99 | 1608[0603]_M | 1

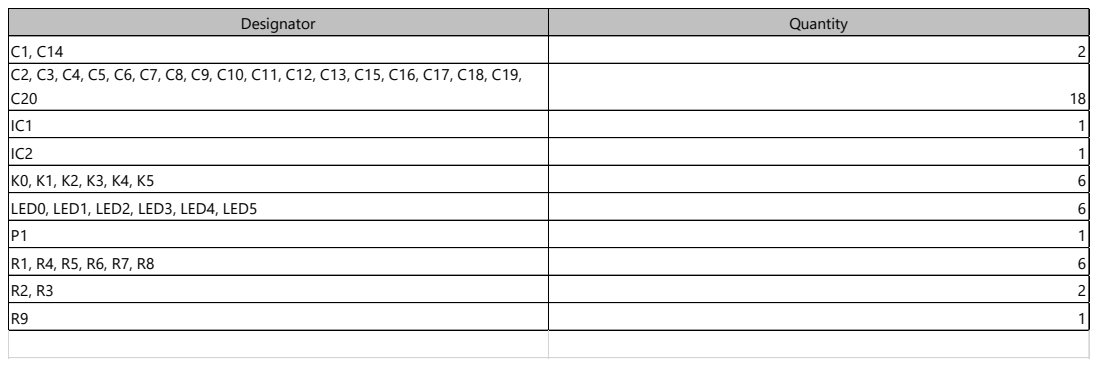
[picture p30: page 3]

Designator | Quantity

C1, C14 | 2
C2, C3, C4, C5, C6, C7, C8, C9, C10, C11, C12, C13, C15, C16, C17, C18, C19, C20 | 18

LED0, LED1, LED2, LED3, LED4, LED5 | 6

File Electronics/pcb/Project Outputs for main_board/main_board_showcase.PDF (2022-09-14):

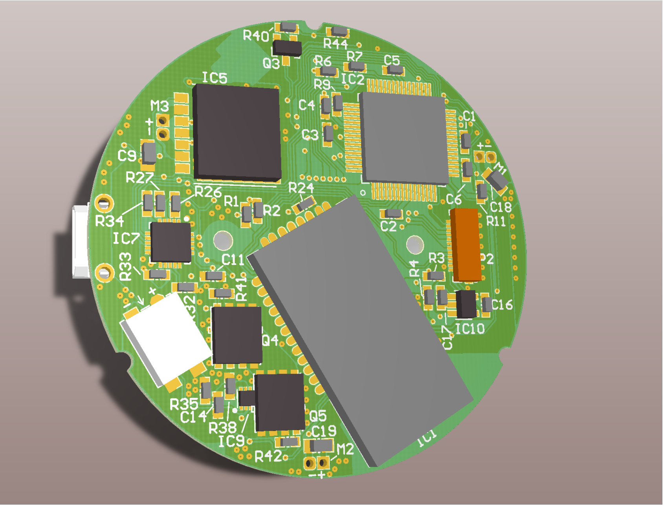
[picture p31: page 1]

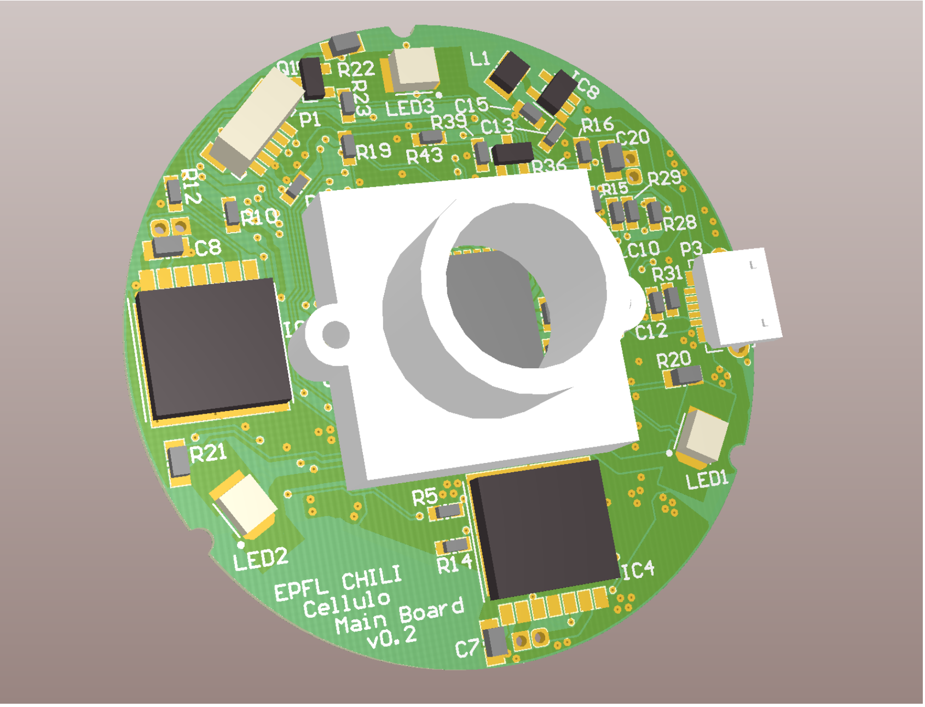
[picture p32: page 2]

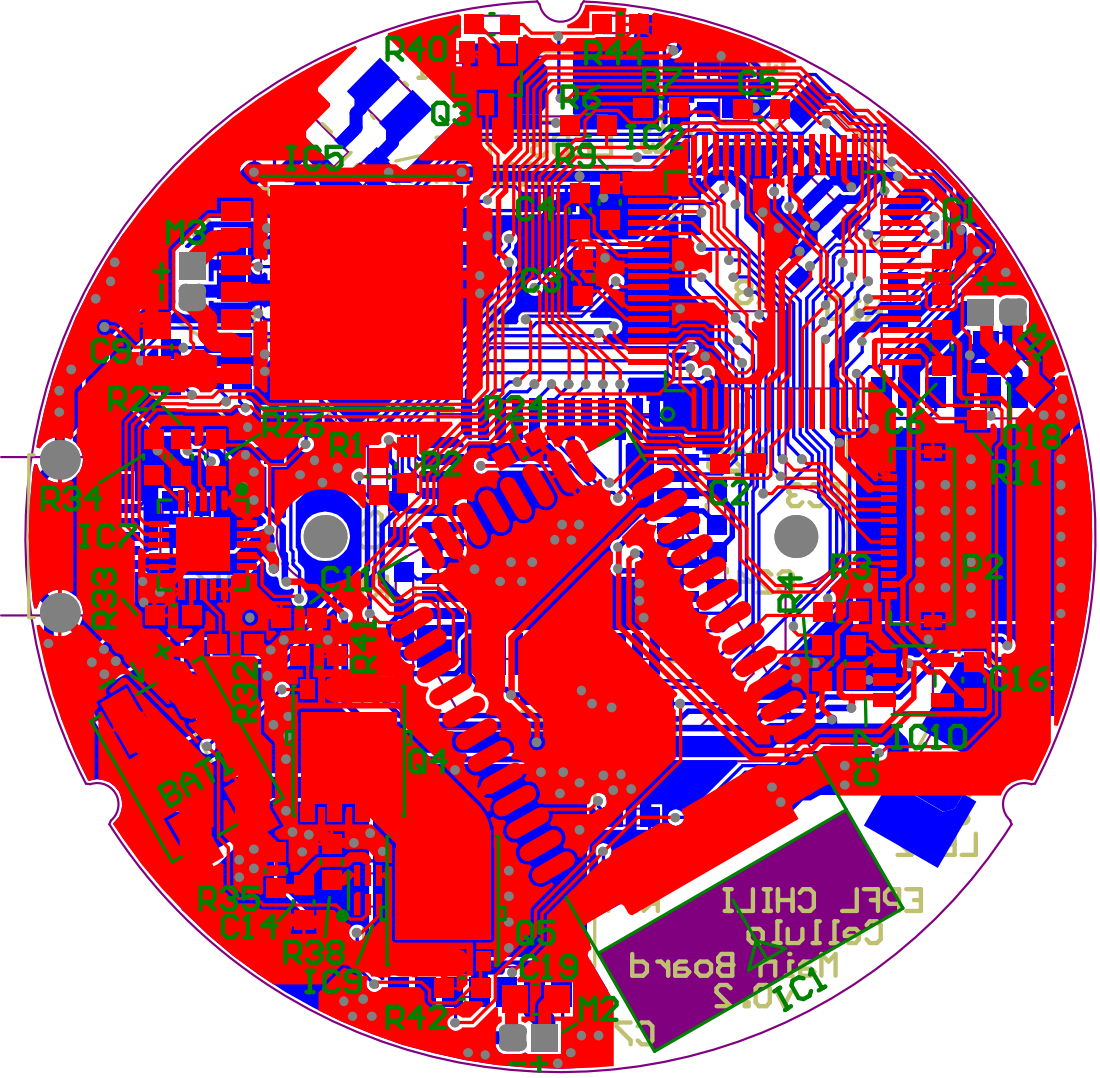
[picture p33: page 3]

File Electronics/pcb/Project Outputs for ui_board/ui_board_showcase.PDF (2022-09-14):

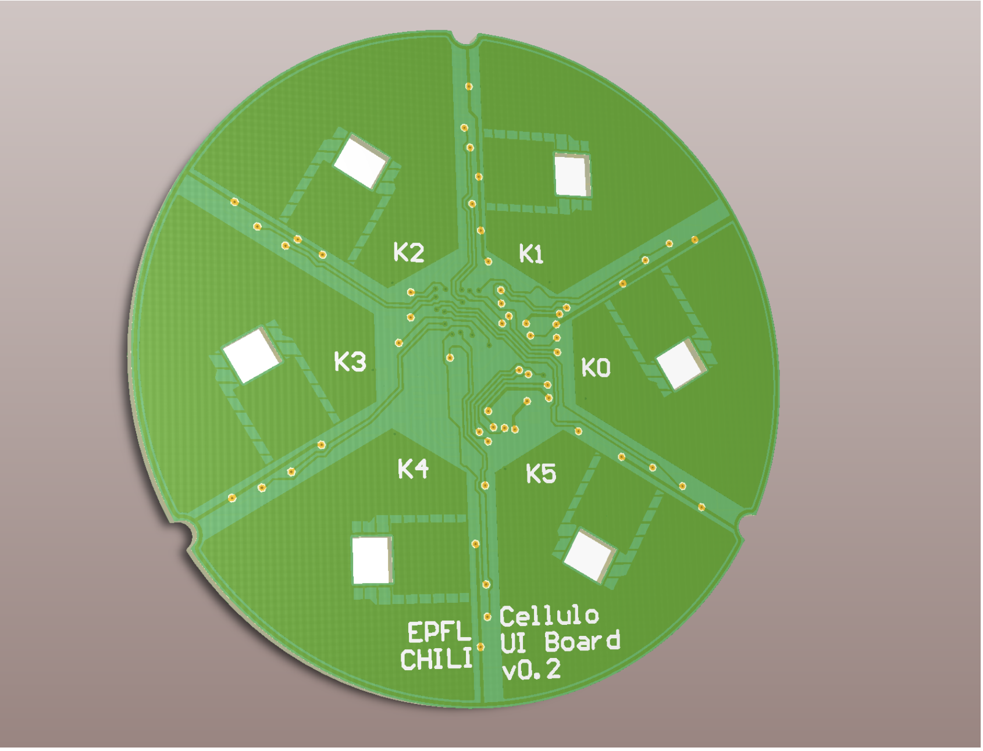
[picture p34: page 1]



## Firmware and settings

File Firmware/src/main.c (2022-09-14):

/*
 * Copyright (C) 2015 EPFL
 *
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
 * You should have received a copy of the GNU General Public License
 * along with this program.  If not, see http://www.gnu.org/licenses/.
 */

/**
 * @file main.c
 * @brief Source for entry point
 * @author Ayberk Özgür
 * @date 2015-05-28
 */

#include <stddef.h>                     // Defines NULL
#include <stdbool.h>                    // Defines true
#include <stdlib.h>                     // Defines EXIT_FAILURE
#include "system/common/sys_module.h"

#include "power.h"
#include "timer.h"
#include "battery.h"
#include "led.h"

#include "cam.h"
#include "bluetooth.h"
#include "touch.h"
#include "gesture.h"
#include "localization.h"
#include "watchdog.h"
#include "motor.h"
#include "motion.h"

int main(void){
    SYS_Initialize(NULL);

    APP_Power_Initialize();

    APP_Timer_Initialize();

    APP_Battery_Initialize();

    APP_BT_Initialize();

    APP_LED_Initialize();

    APP_Cam_Initialize();

    APP_Touch_Initialize();

    APP_Gesture_Initialize();

    APP_Localization_Initialize();

    APP_Motor_Initialize();

    APP_Motion_Initialize();

    SYS_INT_SourceEnable(INT_SOURCE_EXTERNAL_3);
    SYS_INT_SourceEnable(INT_SOURCE_EXTERNAL_4);

    bluetoothEventBootComplete();

    reportActivity();

    APP_Watchdog_Initialize();

    while(true){
        SYS_Tasks();

        APP_Power_Tasks();

        APP_Timer_Tasks();

        APP_Battery_Tasks();

        APP_BT_Tasks();

        APP_LED_Tasks();

        APP_Cam_Tasks();

        APP_Touch_Tasks();

        APP_Gesture_Tasks();

        APP_Localization_Tasks();

        APP_Motor_Tasks();

        APP_Motion_Tasks();

        APP_Watchdog_Tasks();
    }

    return (EXIT_FAILURE);
}

static unsigned int _excep_code;
static unsigned int _excep_addr;
void _general_exception_handler(void){
    asm volatile ("mfc0 %0,$13" : "=r" (_excep_code));
    asm volatile ("mfc0 %0,$14" : "=r" (_excep_addr));

}

void _simple_tlb_refill_exception_handler(void){
}

void _cache_err_exception_handler(void){
}

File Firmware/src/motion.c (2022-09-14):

/*
 * Copyright (C) 2015 EPFL
 *
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
 * You should have received a copy of the GNU General Public License
 * along with this program.  If not, see http://www.gnu.org/licenses/.
 */

/**
 * @file motion.c
 * @brief Source for motion control
 * @author Ayberk Özgür
 * @date 2015-12-14
 */

#include "motion.h"

#include <math.h>

#include "haptics.h"
#include "bluetooth.h"
#include "bezier.h"

#define abs(X) ((X) >= 0 ? (X) : -(X))
#define max(X,Y) ((X) > (Y) ? (X) : (Y))
#define PI 3.14159265359f

MOTION_TRACKER currentMotionTracker = MOTION_TRACKER_NONE; ///< Currently active tracker

LocomotionInteractivityMode locomotionInteractivityMode = LocomotionInteractivityModeNormal;

int goalPoseX = 0;
int goalPoseY = 0;
int goalPoseTheta = 0;
float goalPoseMaxV = 0.0;
float goalPoseMaxW = 0.0;

int polyBezierAlignedTheta = 0;

const float pPoseXY = 2.0f;             ///< Proportional component of goal pose controller for x and y
const float pPoseTheta = 0.1f;          ///< Proportional component of goal pose controller for theta
const float pPoseThetaGoalless = 0.08f; ///< Proportional component of goal pose controller for theta, when there is no fixed goal

const float marginXY = 5.0f;            ///< Within this bound of x and y, we consider we reached the goal
const float marginTheta = 2.0f;         ///< Within this bound of theta, we consider we reached the goal

bool xGoalReached = false;              ///< Whether we are within marginXY of the x goal
bool yGoalReached = false;              ///< Whether we are within marginXY of the y goal
bool thetaGoalReached = false;          ///< Whether we are within marginTheta of the theta goal
bool polyBezierGoalReached = false;     ///< Whether the composite Bézier curve is entirely tracked
bool relevantGoalsReached = false;      ///< Whether all coordinate components relevant to the current tracker are within margins

const short motorOutputMax = 0xFFF;     ///< Maximum motor output, absolute value
const short motorOutputMin = 0x420;     ///< Minimum motor output, absolute value

short motor1Target = 0;                 ///< Target output for motor 1
short motor2Target = 0;                 ///< Target output for motor 2
short motor3Target = 0;                 ///< Target output for motor 3

float vxGlobalMeasured = 0.0;
float vyGlobalMeasured = 0.0;
float vxLocalMeasured = 0.0;
float vyLocalMeasured = 0.0;
float wrMeasured = 0.0;
float wMeasured = 0.0;
float v1Measured = 0.0;
float v2Measured = 0.0;
float v3Measured = 0.0;
float vxGlobalMeasuredSmoothed = 0.0;
float vyGlobalMeasuredSmoothed = 0.0;
float wMeasuredSmoothed = 0.0;

float vxGlobalGoalTracker = 0.0; ///< Global Vx goal dictated by the active tracker
float vyGlobalGoalTracker = 0.0; ///< Global Vy goal dictated by the active tracker
float wGlobalGoalTracker = 0.0;  ///< Global w goal dictated by the active tracker

int prevPoseX = 0;
int prevPoseY = 0;
float prevPoseThetaRad = 0;
unsigned int prevPoseTimestamp = 0;

float k_inv[9] = {
    0.666666666666667f,     0.0f,                   0.333333333333333f,
    -0.333333333333333f,    0.577350269189626f,     0.333333333333333f,
    -0.333333333333333f,    -0.577350269189626f,    0.333333333333333f
}; ///< Inverse kinematic transfer matrix: Maps x, y, theta velocities to wheel velocities

void setLocomotionInteractivityMode(LocomotionInteractivityMode newMode){
    locomotionInteractivityMode = newMode;
}

void setGoalPose(int x, int y, int theta, float v, float w){
    goalPoseX = x;
    goalPoseY = y;
    goalPoseTheta = theta;
    goalPoseMaxV = v;
    goalPoseMaxW = w;
    currentMotionTracker = MOTION_TRACKER_POSE;
    relevantGoalsReached = false;
    //***************************** CLEAR D AND I
}

void setGoalPosition(int x, int y, float v){
    goalPoseX = x;
    goalPoseY = y;
    goalPoseMaxV = v;
    goalPoseMaxW = 0;
    currentMotionTracker = MOTION_TRACKER_POSITION;
    relevantGoalsReached = false;
    //***************************** CLEAR D AND I
}

void setGoalXCoordinate(int x, float v){
    goalPoseX = x;
    goalPoseMaxV = v;
    goalPoseMaxW = 0;
    currentMotionTracker = MOTION_TRACKER_X_COORDINATE;
    relevantGoalsReached = false;
    //***************************** CLEAR D AND I
}

void setGoalYCoordinate(int y, float v){
    goalPoseY = y;
    goalPoseMaxV = v;
    goalPoseMaxW = 0;
    currentMotionTracker = MOTION_TRACKER_Y_COORDINATE;
    relevantGoalsReached = false;
    //***************************** CLEAR D AND I
}

void setGoalOrientation(int theta, float w){
    goalPoseTheta = theta;
    goalPoseMaxV = 0;
    goalPoseMaxW = w;
    currentMotionTracker = MOTION_TRACKER_ORIENTATION;
    relevantGoalsReached = false;
    //***************************** CLEAR D AND I
}

void setGoalXThetaCoordinate(int x, int theta, float v, float w){
    goalPoseX = x;
    goalPoseTheta = theta;
    goalPoseMaxV = v;
    goalPoseMaxW = w;
    currentMotionTracker = MOTION_TRACKER_X_THETA_COORDINATE;
    relevantGoalsReached = false;
    //***************************** CLEAR D AND I
}

void setGoalYThetaCoordinate(int y, int theta, float v, float w){
    goalPoseY = y;
    goalPoseTheta = theta;
    goalPoseMaxV = v;
    goalPoseMaxW = w;
    currentMotionTracker = MOTION_TRACKER_Y_THETA_COORDINATE;
    relevantGoalsReached = false;
    //***************************** CLEAR D AND I
}

void setGoalVelocity(float vx, float vy, float w){
    vxGlobalGoalTracker = vx;
    vyGlobalGoalTracker = vy;
    wGlobalGoalTracker = w;
    currentMotionTracker = MOTION_TRACKER_VELOCITY;
    //***************************** CLEAR D AND I
}

void setGoalPolyBezier(float v, float w){
    goalPoseMaxV = v;
    goalPoseMaxW = w;
    currentMotionTracker = MOTION_TRACKER_POLYBEZIER;
    relevantGoalsReached = false;
    //***************************** CLEAR D AND I
    polyBezierTrackerState = POLYBEZIER_TRACKER_GOING_TO_START;
    getPolyBezierInit(&goalPoseX, &goalPoseY);
}

void setGoalPolyBezierAligned(float v, int theta, float w){
    goalPoseMaxV = v;
    goalPoseMaxW = w;
    polyBezierAlignedTheta = theta;
    currentMotionTracker = MOTION_TRACKER_POLYBEZIER_ALIGNED;
    relevantGoalsReached = false;
    //***************************** CLEAR D AND I
    polyBezierTrackerState = POLYBEZIER_TRACKER_GOING_TO_START;
    getPolyBezierInit(&goalPoseX, &goalPoseY);
}

void clearTracking(){
    goalPoseX = 0;
    goalPoseY = 0;
    goalPoseTheta = 0;
    goalPoseMaxV = 0;
    goalPoseMaxW = 0;
    currentMotionTracker = MOTION_TRACKER_NONE;
}

/**
 * @brief Sets all measured velocities to zero
 */
inline void zeroMeasuredVelocities(){
    vxGlobalMeasured = 0.0;
    vyGlobalMeasured = 0.0;
    vxLocalMeasured = 0.0;
    vyLocalMeasured = 0.0;
    wrMeasured = 0.0;
    wMeasured = 0.0;
    v1Measured = 0.0;
    v2Measured = 0.0;
    v3Measured = 0.0;
}

/**
 * @brief Sets all motor outputs to zero
 */
inline void zeroMotorOutputs(){
    setMotorOutput(1, 0);
    setMotorOutput(2, 0);
    setMotorOutput(3, 0);
}
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

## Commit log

2022-09-14 Update main folders
    [3-ball-drive-housing-bottom.STL, 3-ball-drive-housing-top.STL, 3-ball-drive.SLDASM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]
2022-12-02 mount and firmware flashing videos added

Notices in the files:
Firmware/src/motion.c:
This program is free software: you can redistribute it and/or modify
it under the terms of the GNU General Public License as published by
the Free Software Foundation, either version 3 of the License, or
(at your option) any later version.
